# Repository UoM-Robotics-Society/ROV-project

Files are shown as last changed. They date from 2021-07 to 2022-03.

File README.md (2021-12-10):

# ROV-project

## Description 
This repository contains the software, hardware and 3D design for the ROV project.

## Project introduction and motivation
Goal is to create Remotely Operated Vehicle for underwater environments. ROV should :
- should operate safely in underwater environment up to reasonably low water depth ( construction should be waterproof, designed in mind to deal with the possibility of flooding)
- be able to be controlled by the User on ground station ( using something like GUI or physical devices like joystick/xbox controller etc. )
- provide useful data from sensors to User ( video feedback, attitude ( orientation ), other somehow relevant sensors )
- design should be flexible for possible modification in future 

## Diagram 
Whole system of the ROV is presented on the image below :
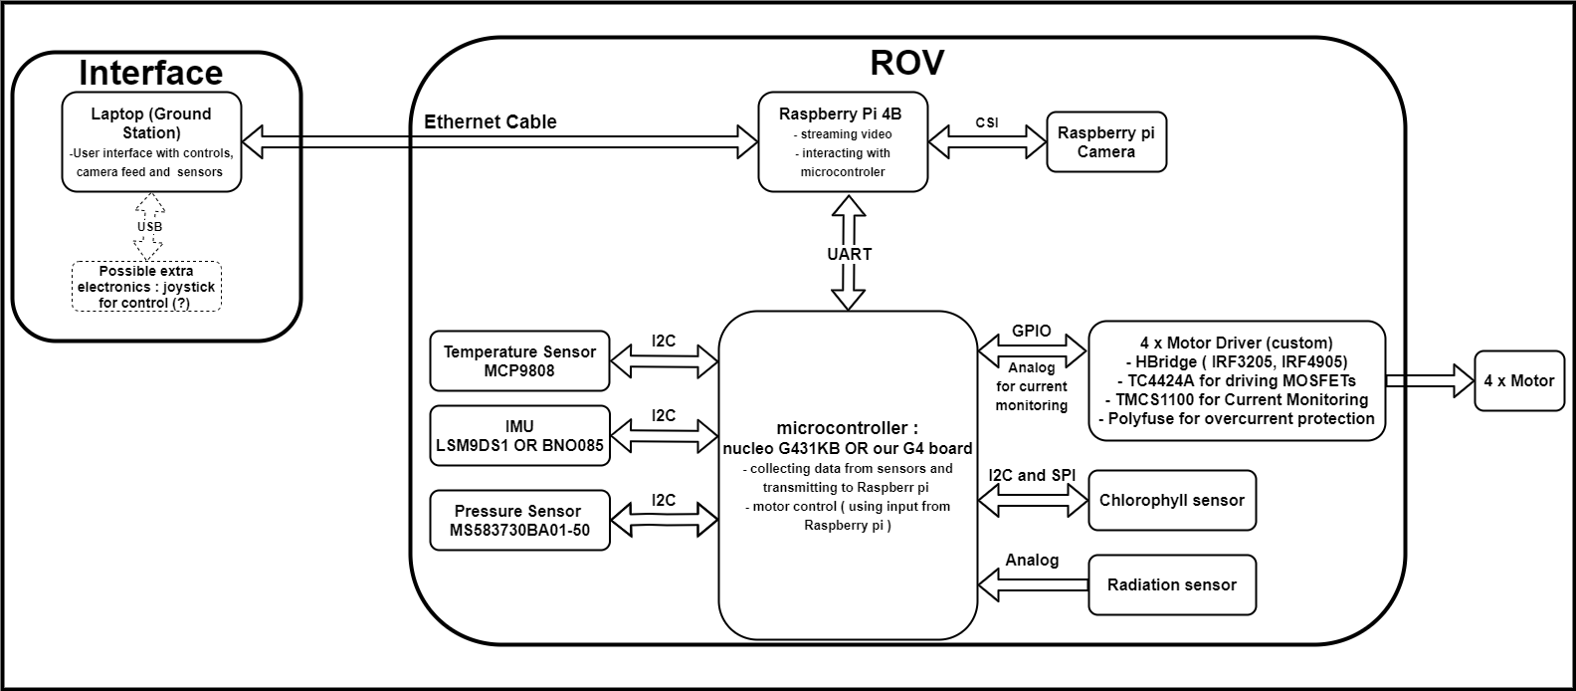
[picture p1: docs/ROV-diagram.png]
diagram


## Mechanical Design 
### Design
video of the model render

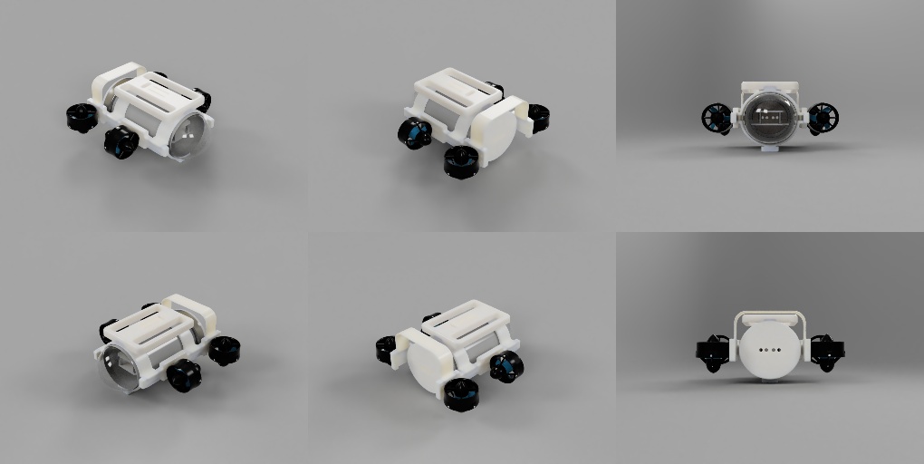
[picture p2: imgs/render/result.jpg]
stiched images of the mode


whole mechanical design is done by mechanical team of ROV team  
### Waterproofing

### Components Description 
#### Ground Station
- Main device with which User will interact will be laptop ( or other device to which we can connect Ethernet cable and will provide easy interaction ). Using laptop/other workstation provides few benefits : 
    - Most of the "heavy stuff" will be done on the workstation that we can control and only necessary software will run in the actual ROV 
    - makes the system very flexible : lots of possible expansion in the future ( fancy control like joysticks ? We can create own device and plug to USB or add support for xbox controller. Some computer vision algorithms for the camera ? the workstation can have GPU on it, we can provide quite a lot of computation power ( rather than relying on raspberry pi or other single board computer ))

#### Communication
- Ethernet should allow fast ( Raspberry pi has 1Gbit Ethernet port ), reliable and long distance communication ( and works underwater since it's just a cable ). We can also use Ethernet to power the device ( "Power over Ethernet") 
-  All other communication within ROV uses standard and popular data transmission protocols 
-  According to David, possiblity of extension to wireless 

Raspberry pi connected to laptop over 20 meter ethernet cable. Currently just streams video ( 1080p) over MQTT, bandwidth test below : 
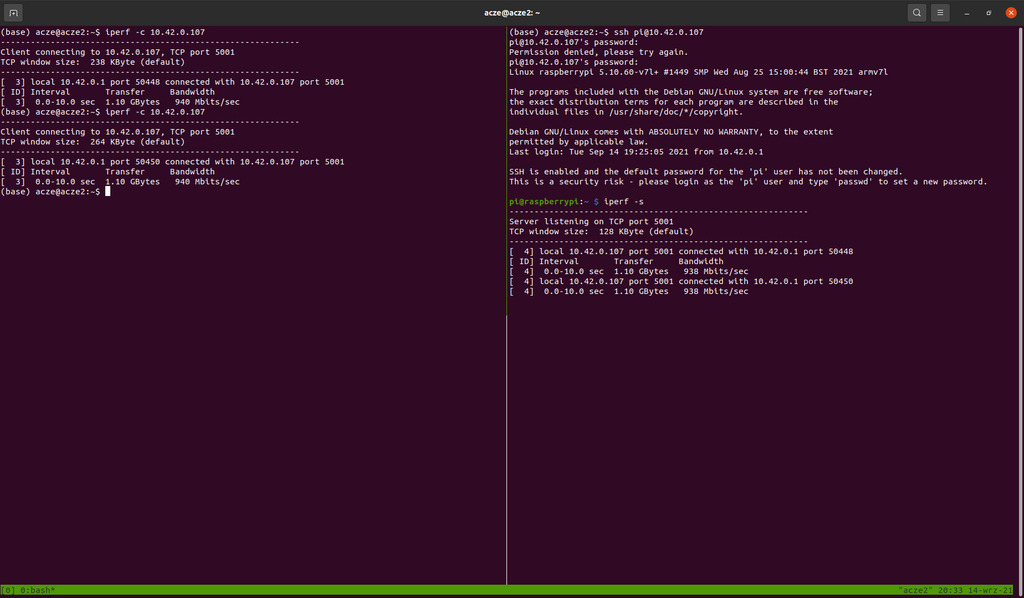
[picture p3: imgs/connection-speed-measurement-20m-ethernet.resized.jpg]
940 Mbit/s for communication


### Single Board Computer ( Raspberry Pi 4b)
- Extremely popular platform with support for good quality, real time video streaming and interacting with hardware ( using Serial communication ). Great community support and very fast to learn ( also Computer Science departament uses it in teaching )
- Can be programmed in few languages ( C, C++, python, probably others ), although python is used for the fast and easy development ( limitations of python like GIL can be removed by using multiprocessing etc.). 

### Microcontroller ( STM32G4)
- Microcontroller from new G4 line from STMicroelectronics. Not popular line, not "battle-tested" but cheap, high-performance microcontroller with lots of peripherals and can be programmed in Mbed Environment or HAL. Although there are popular choices ( pico's, arduino atmega's, ESP32's other stm's) it can be great opportunity to learn new platform that seems to be targeted for more industrial applications ( and overall learn something new and fun). Other than that, it has lots of features per pound ( 3.5 pound before chip shortage). The design doesn't realy that much on the microcontroller ( it requires few good timers, I2C, UART, SPI, reasonable ADC, most of the microcontrollers provide that)  so we can change to other platform if the chosen microcontroller won't prove it's worth. 

Current microcontroller board :<br>
STM32 G4 board
<br><br>
Render of the final board that will go hopefully in the final design
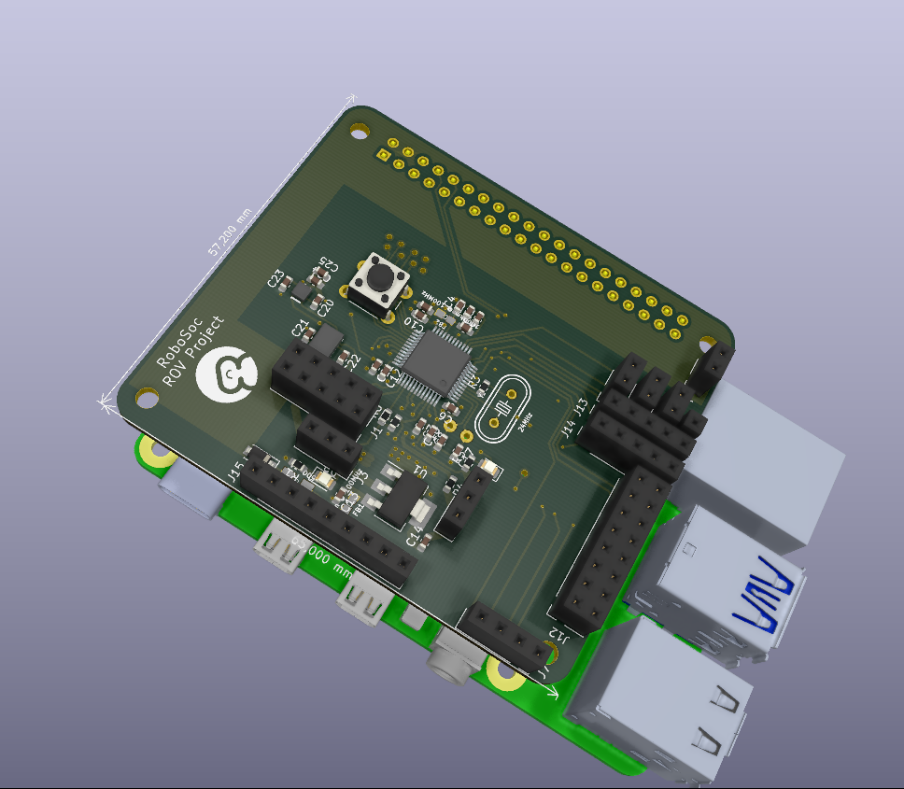
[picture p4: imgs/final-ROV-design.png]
STM32 G4 board


### Motors
- Lots of possible choices ( We orderd the dual shaft ,mabuchi like(DC motor),~30W from robotshop). Custom driver created for the motors using Hbridge circuit. Main drawback is that we need to solder/design/debug it but advantage is that it provides quite a bit of extra features that we included in our design : overcurrent protection ( using polyfuse ), high amperage and reasonably low power losses ( dependent on mosfets ), protection of Microcontroller pins ( using Mosfet driver to drive large mosfets from Hbridge) and current monitoring ( output voltage of TMCS1100 sensor is proportional to the current that flows through the mosfets). All of the features could possibly help us debugging, monitoring and hopefully help with safety when dealing with large motors.
-  Possibility of adding encoders in the future 

Current Motor driver : <br>
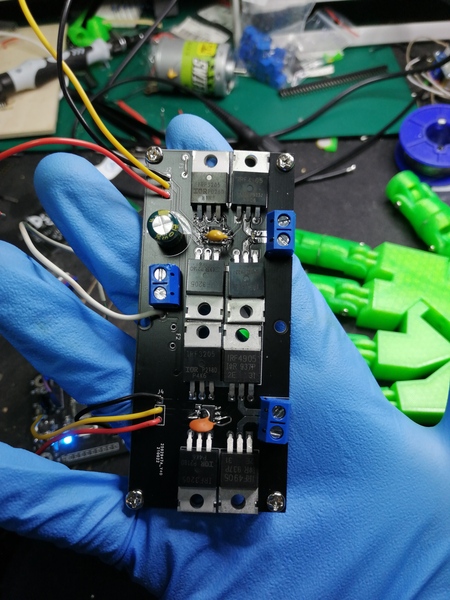
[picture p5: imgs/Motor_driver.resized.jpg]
Motor driver


### Sensors 
- Other than driving platform we wanted to provide range of measurements:
  -  Temperature sensor is standard. 
  -  Pressure sensor is not popular sensor, designed specifically for underwater environment ( up to 300m ) which provides high resolution ( and it's low cost compared to other underwater sensors ). 
  -  MARG sensor ( accelerometer, gyroscope, magnetometer). Using the data we can use AHRS algorithm ( experimented with Madgwick Filter which will be probably used in the design) we can visualize the orientation of the ROV on display on the laptop / ground station [Madgwick Report](https://www.x-io.co.uk/res/doc/madgwick_internal_report.pdf).
  -  Chlorophyll sensor. Custom sensor using the fluorescence measurement that should allow us to estimate the chlorophyll concentration. Chlorophyll concentration helps scientists to estimate health of the lake/other water containers [TODO point to document with more details].
  -  Radiation sensor : was in the first design because of initial project idea from Sellafield. Seems like challenging project and cool expansion to the project. Initial design created from the Elektor magazine article about Radiation detection. General reference used for it was "Radiation detection and measurement" and [opengeiger](http://www.opengeiger.de/index_en.html) website

Sensors : <br>
Chlorophyll sensor : <br>
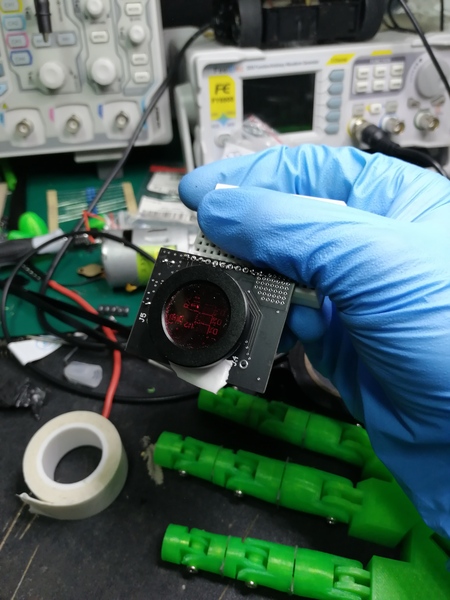
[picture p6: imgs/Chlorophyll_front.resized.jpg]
Chlorophyll sensor front

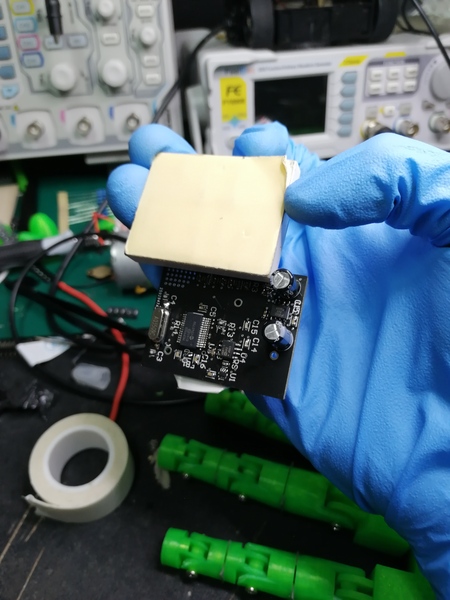
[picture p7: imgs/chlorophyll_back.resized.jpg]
Chlorophyll sensor back


Pressure Sensor : <br>
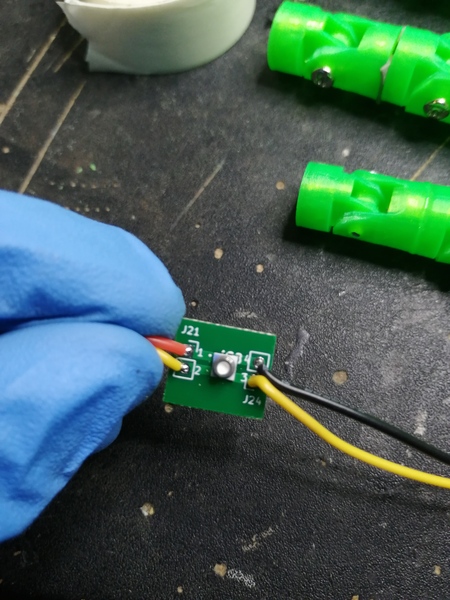
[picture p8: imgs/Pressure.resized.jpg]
Pressure sensor


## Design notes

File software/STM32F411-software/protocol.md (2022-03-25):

## Serial communication with the STM32 

|1 Byte | 2 Byte |3 Byte|4 Byte|
|---|---|---|---|
|peripheral|config|data[15:7]|data[7:0]|

### Peripheral
|Peripherals|
|---|
| 0x00 : STM32 config | 
| 0x01 : Motor Control |
| 0x02 : LED |
| 0x03: Leak detection |
| 0x04 : Temperature sensor |
| 0x05 : Pressure sensor |
| 0x06 : Radiation sensor |
| 0x07 : chlorophyll sensor |

### Config
|7th bit|6th bit|5th bit|4th bit|3th bit|2th bit|1th bit|0th bit|
|---|---|---|---|---|---|---|---|
|Write 0<br>Read 1|type bit 1|type bit 0|channel bit 4|channel bit 3|channel bit 2|channel bit 1|channel bit 0|

### Examples
|command|purpose|CLI command|
|---|---|---|
|0x00, 0b00000000, 0x00, 0x00| echo|stm32 write 0 0 0| 
|0x00, 0b00000001, 0x00, 0x01| toggle LED|stm32 write 0 1 0|
|0x01, 0b00000000, 0x00, 0x00| write x to motor channel 0|motor write 0 0 x| 
|0x01, 0b00000001, 0x00, 0x00| write x to motor channel 1|motor write 0 1 x| 
|0x01, 0b00000010, 0x00, 0x00| write x to motor channel 2|motor write 0 2 x| 

    STM32 Config
        Channel : 0
            description : Echo back the message
        Channel : 1
            description : Toggle LED
            data:
                0 : turn off the LED
                1 : turn on  the LED
                2 : toggle the LED 
        Channel : 2
            description:
    Motor Control:
        Channel : 0
            description : Thruster nr 1
            Type:
                0 : write value to CRT
                1 : data represents x / 10000 of duty cycle ( max x = 10000. 100% duty cycle
                2 : set frequency
            data:
                interpretation dependent on type above
        Channel : 1
            description : Thruster nr 2
            Type:
                0 : write value to CRT
                1 : data represents x / 10000 of duty cycle ( max x = 10000. 100% duty cycle
                2 : set frequency
            data:
                interpretation dependent on type above
        Channel : 2
            description : Thruster nr 3
            Type:
                0 : write value to CRT
                1 : data represents x / 10000 of duty cycle ( max x = 10000. 100% duty cycle
                2 : set frequency
            data:
                interpretation dependent on type above
        Channel : 3
            description : Thruster nr 4
            Type:
                0 : write value to CRT
                1 : data represents x / 10000 of duty cycle ( max x = 10000. 100% duty cycle
                2 : set frequency
            data:
                interpretation dependent on type above
    LED Control:
        Channel 0:
            description : control of while LED 1 
            Type : 
                0 : write value to CRT
                1 : 
            data:
                decrpition: interpretation depends on the type

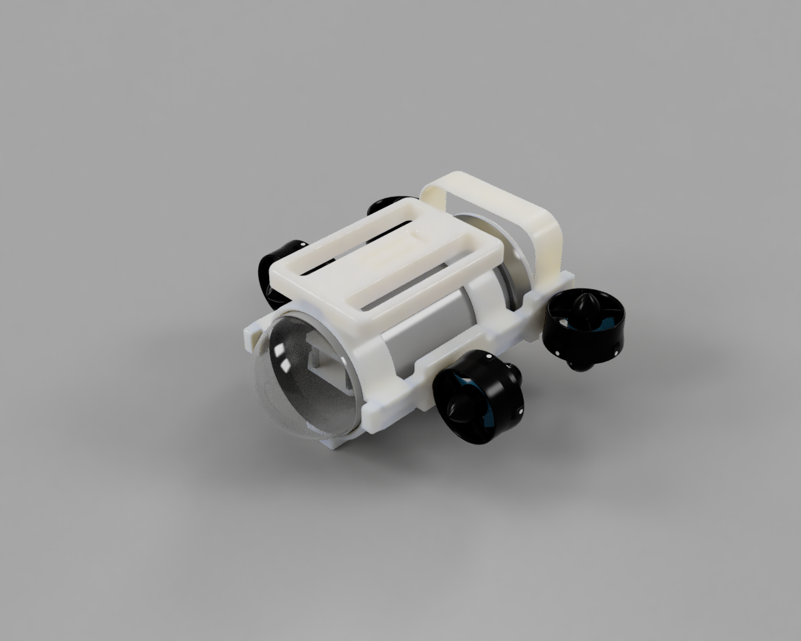
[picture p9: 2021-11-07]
imgs/pres/Front_Right.png

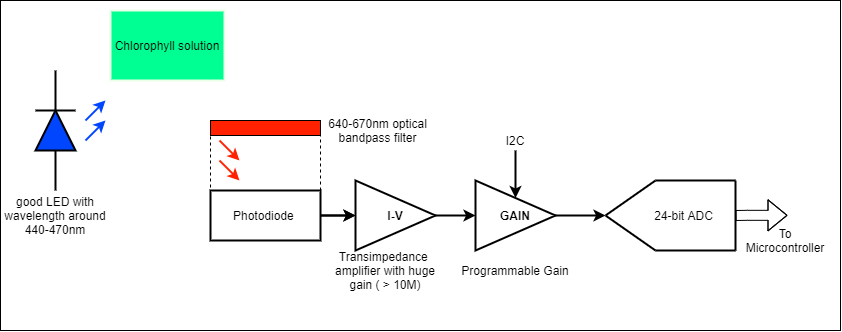
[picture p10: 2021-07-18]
docs/chlorophyll-sensor.png

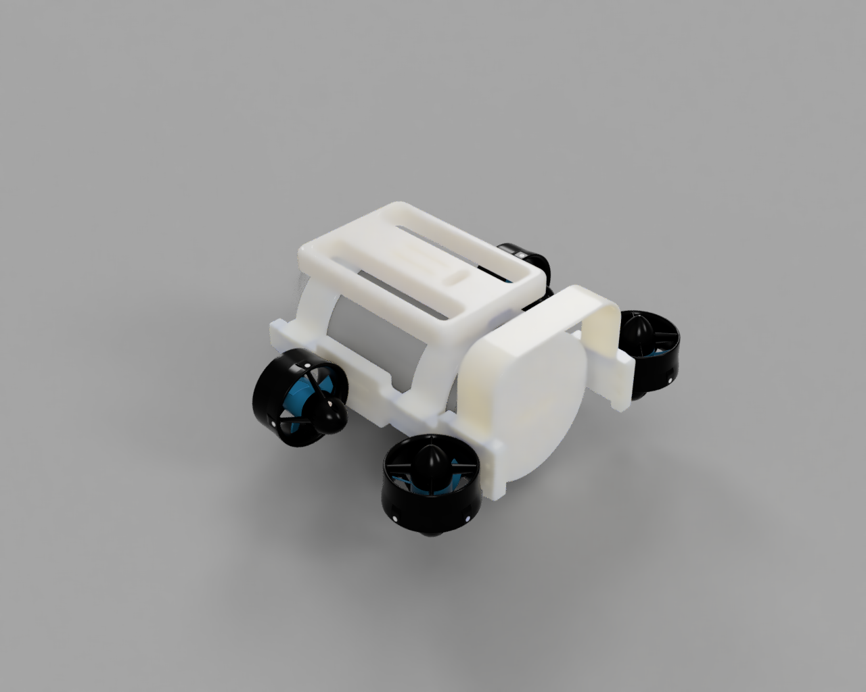
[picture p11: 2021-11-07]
imgs/render/Back_Left.png

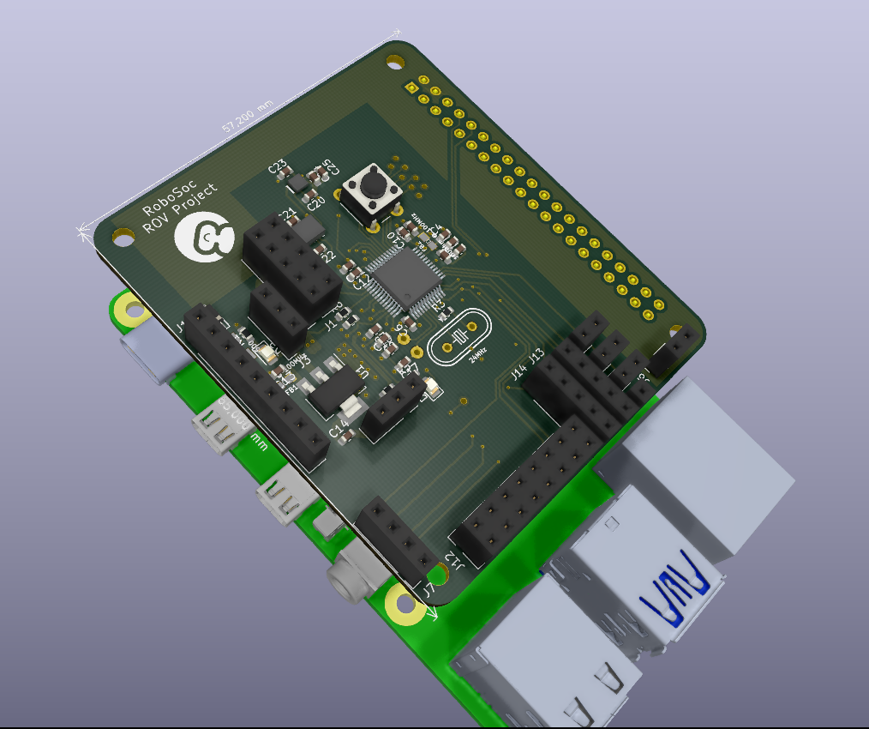
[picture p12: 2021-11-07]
imgs/pres/final_board.png

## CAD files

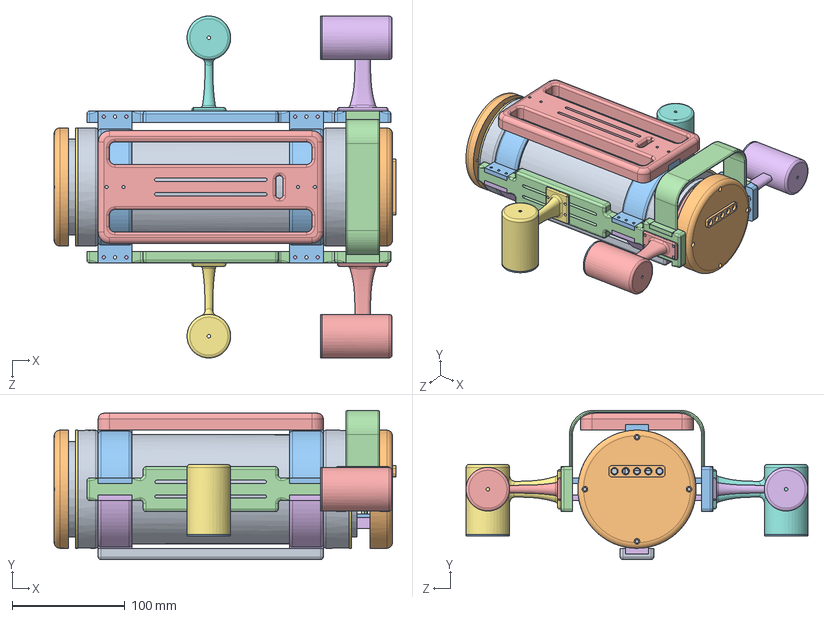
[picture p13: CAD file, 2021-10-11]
mechanical-design/ROV Design/ROV MK 4.SLDASM
303.5 x 132.5 x 303.8 mm
Cylinder Front Lid
Side Frame Right
Side Frame Left
Motor Connector Rod left
Motor Connector Rod Right
Motor Up Connector Rod Left
Motor Up Connector Rod Right
Bottom Frame
Cylinder Back Lid Cap
Cylinder Back Lid Bottom Plate
25 mm Standoff x 4
Cylinder Back Lid Top Plate
Cylinder Back Lid Bottom Plate Holder
Raspberry Standoff x 4
Raspberry Camera Housing
Raspberry Camera
Chlorophyll Sensor
Bracket Holder x 2
Bracket No Holder Back
Bracket Holder Botoom x 2
Rubber seal large 2 x 2
Rubber seal x 2
Glass
Rubber seal medium
Motor Cap x 4

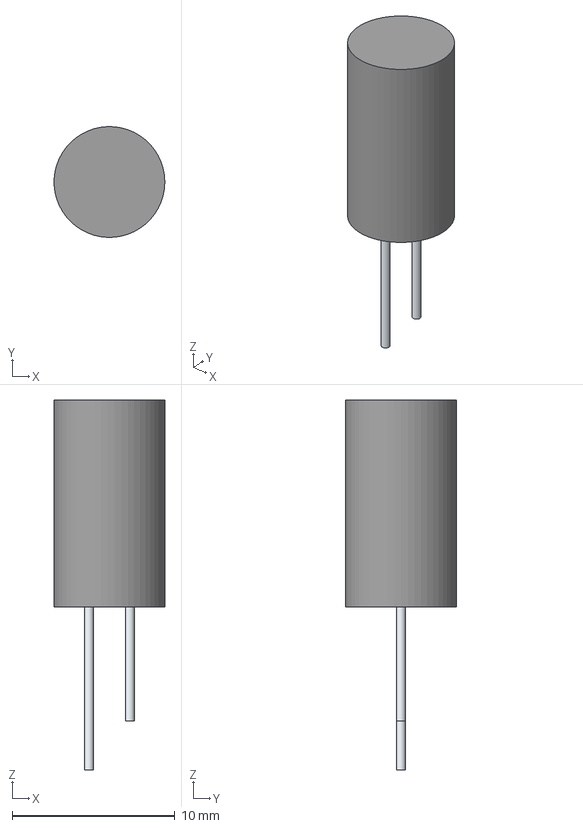
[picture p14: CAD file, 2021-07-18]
hardware/chlorophyll_sensor/design/3d_cad/EEU-FR1E151.stp
6.79 x 6.80 x 22.7 mm
SimpleBody
Pin1
Pin2

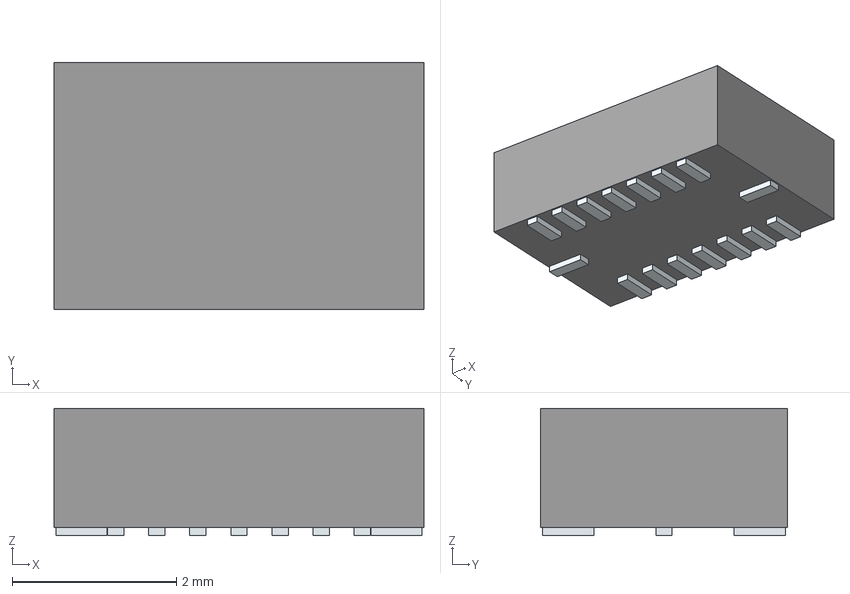
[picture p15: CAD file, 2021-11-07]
hardware/Final-G4-board/3d/BMI088.stp
4.50 x 3.00 x 1.55 mm
Pins

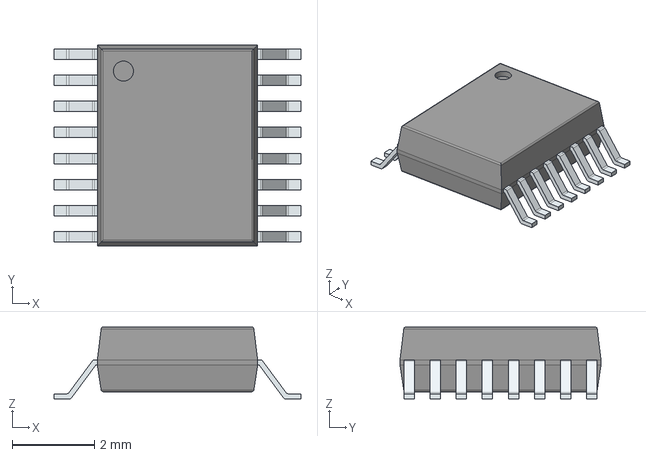
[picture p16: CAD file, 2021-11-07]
hardware/radiation_sensor/extra/3D/LTC6242HVCGN#PBF.stp
6.01 x 4.89 x 1.75 mm
PinsArrayLR

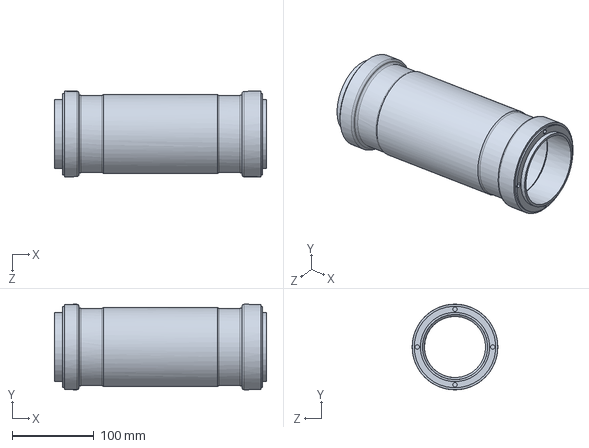
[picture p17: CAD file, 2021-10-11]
mechanical-design/ROV Design/Cylinder.SLDPRT
260.0 x 105.0 x 105.0 mm

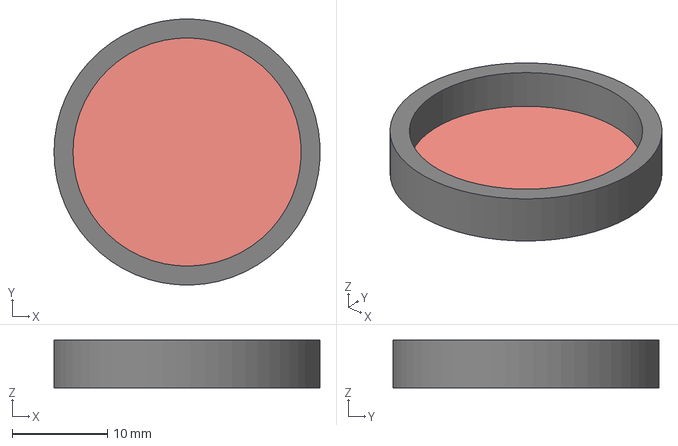
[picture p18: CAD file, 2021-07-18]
hardware/chlorophyll_sensor/design/3d_cad/filter v1.step
28.0 x 28.0 x 5.00 mm

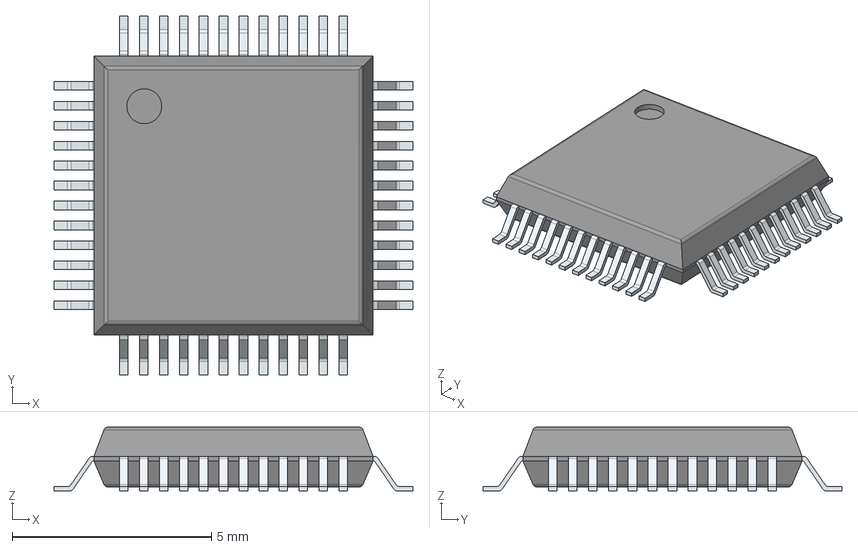
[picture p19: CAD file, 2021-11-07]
hardware/Final-G4-board/3d/STM32G431C6T6.stp
9.00 x 9.00 x 1.60 mm
PinsArrayLR
PinsArrayTB

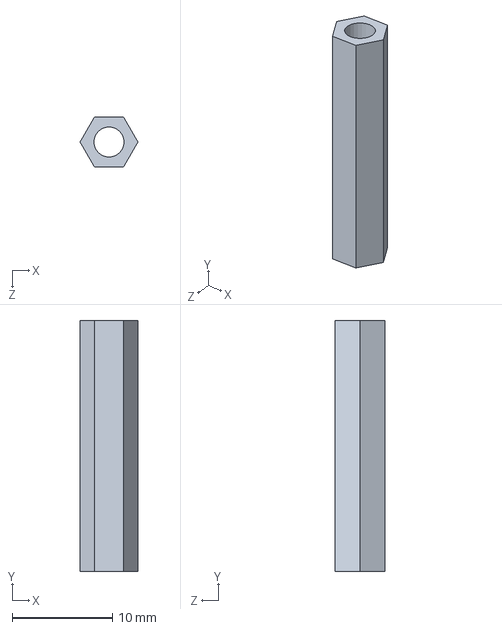
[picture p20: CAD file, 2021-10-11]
mechanical-design/ROV Design/25 mm Standoff.SLDPRT
5.77 x 25.0 x 5.00 mm

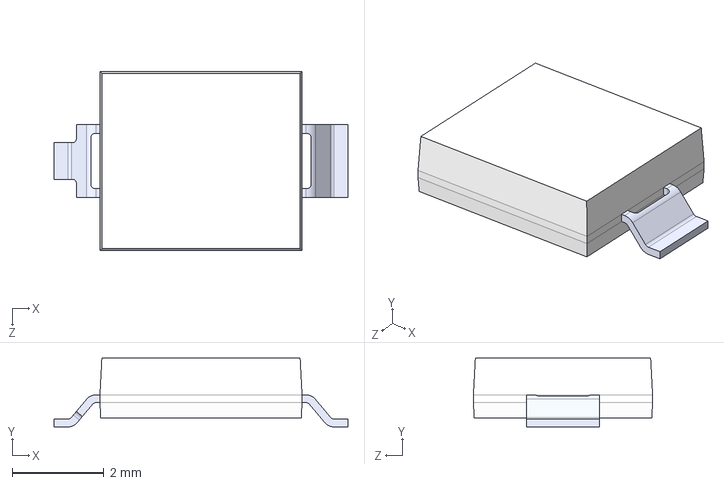
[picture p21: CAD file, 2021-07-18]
hardware/chlorophyll_sensor/design/3d_cad/VBPW34S--3DModel-STEP-56544.STEP
6.40 x 1.50 x 3.90 mm

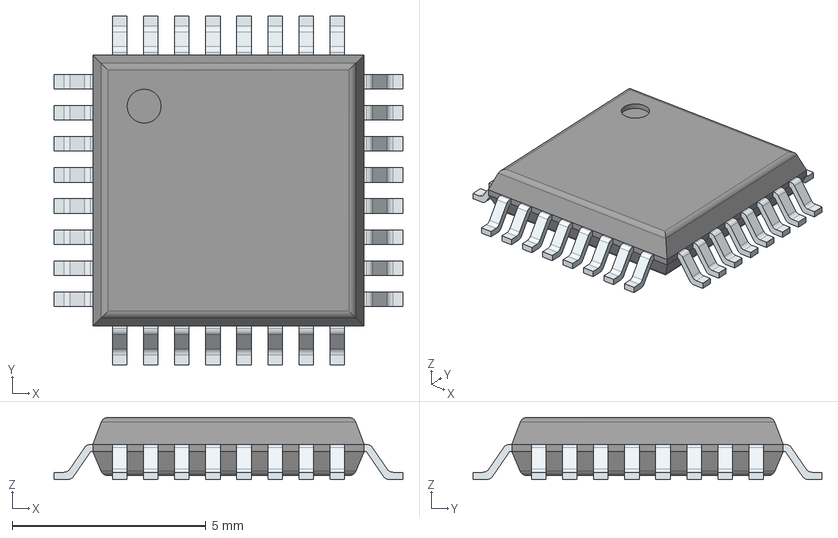
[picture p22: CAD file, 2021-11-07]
hardware/Final-G4-board/3d/STM32G431K8T6.stp
9.00 x 9.00 x 1.60 mm
PinsArrayLR
PinsArrayTB

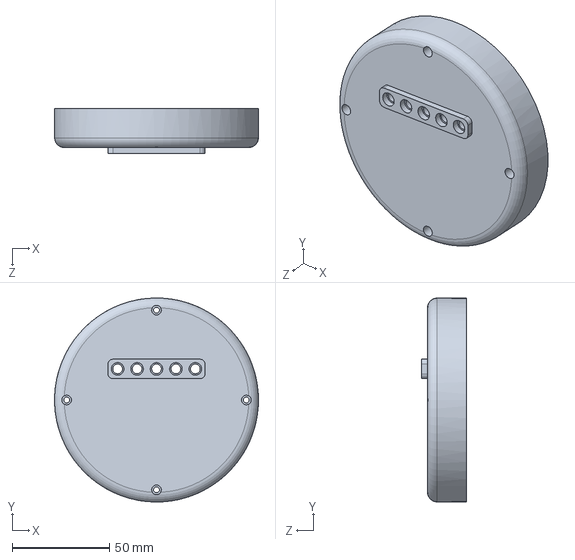
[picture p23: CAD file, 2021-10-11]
mechanical-design/ROV Design/Cylinder Back Lid Cap.SLDPRT
105.0 x 105.0 x 23.0 mm

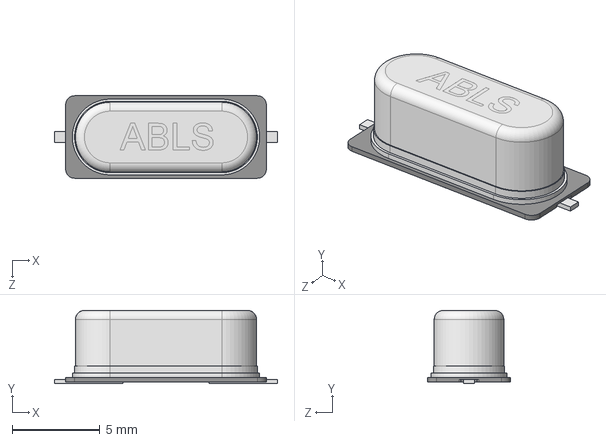
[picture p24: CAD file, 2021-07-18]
hardware/chlorophyll_sensor/design/3d_cad/ABLS.STEP
12.7 x 4.17 x 4.70 mm

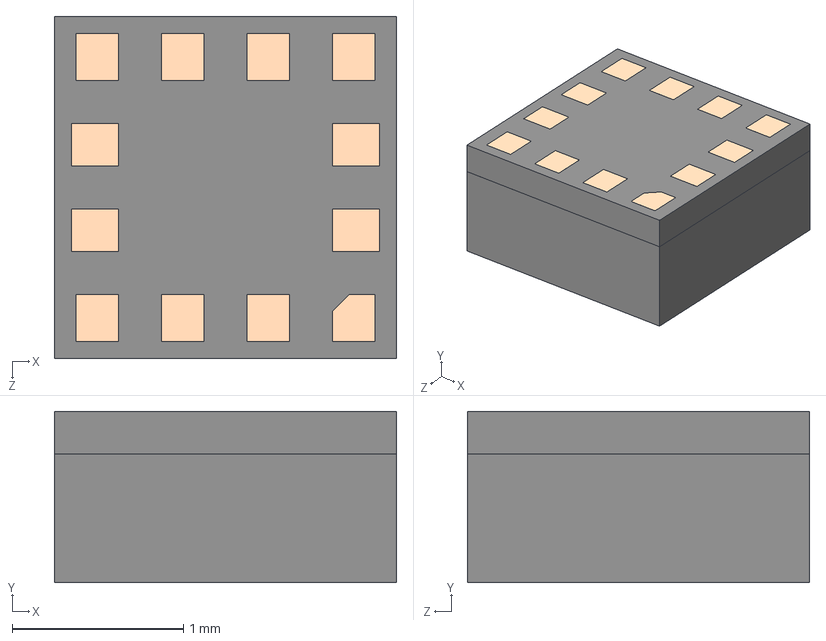
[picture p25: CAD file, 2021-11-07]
hardware/Final-G4-board/3d/LSM303AGRTR.stp
2.00 x 1.00 x 2.00 mm

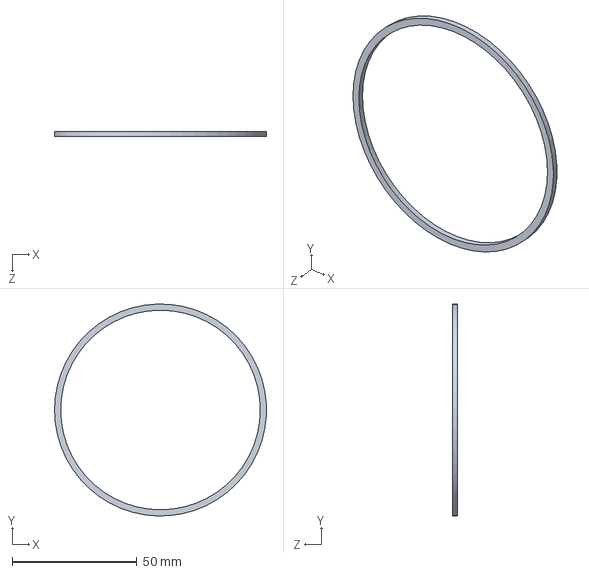
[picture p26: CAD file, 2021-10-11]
mechanical-design/ROV Design/Rubber seal medium.SLDPRT
85.0 x 85.0 x 2.00 mm

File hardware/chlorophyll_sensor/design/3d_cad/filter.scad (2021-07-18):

color("black", 1)
difference()
{
    cylinder(d=28, h=4, $fn=100);
    translate([0,0,-0.1])
    cylinder(d=24, h=4.5, $fn=100);
}

translate([0, 0, 2.7])
color("red", 0.3)
cylinder(d=25,h=1, $fn=100);

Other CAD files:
hardware/chlorophyll_sensor/design/3d_cad/User Library-VEMD1060X01-1.STEP
hardware/Final-G4-board/3d/IIS2MDCTR.stp
mechanical-design/ROV Design/Raspberry Standoff.SLDPRT
hardware/chlorophyll_sensor/design/3d_cad/filter.stl
hardware/chlorophyll_sensor/design/3d_cad/SFH_2713_20200701_geometry.STEP
hardware/chlorophyll_sensor/design/3d_cad/m20-97311xx_asm.stp
hardware/radiation_sensor/extra/3D/LTC6242HVCGN#PBF.stl
mechanical-design/ROV Design/Bottom Frame.SLDPRT
mechanical-design/ROV Design/Bracket Holder Botoom.SLDPRT
mechanical-design/ROV Design/Bracket Holder.SLDPRT
mechanical-design/ROV Design/Bracket No Holder Back.SLDPRT
mechanical-design/ROV Design/Cylinder Back Lid Bottom Plate Holder.SLDPRT
mechanical-design/ROV Design/Cylinder Back Lid Bottom Plate.SLDPRT
mechanical-design/ROV Design/Cylinder Back Lid Top Plate.SLDPRT
mechanical-design/ROV Design/Cylinder Front Lid.SLDPRT
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

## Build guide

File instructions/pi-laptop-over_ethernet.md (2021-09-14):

# Connecting
1. Connect via Ethernet cable pi and laptop
2. Settings -> Network -> Wired Gearbox -> IPv4 -> Shared to other computers
3. ```ip a ```  and get the ip address from ethernet interface
3. ```nmap -n -sP 10.42.0.255/24``` ( or any other address)
4. get the ip address from above and ```ssh pi@<ip address of above>```

# Bandwidth test
1. ```sudo apt-get install iperf```
2. On raspberry pi ```iperf -s```
3. On laptop ```iperf -c <ip address of raspberry pi>```

# Results 

|Cabel Length|Bandidth|
|---|---|
|0.25m|942 Mbits/sec|
|20m|940 Mbits/sec|

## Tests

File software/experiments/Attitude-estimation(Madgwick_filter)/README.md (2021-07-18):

# IMU [ Work in progress ] !
playing with 3d attitude estimation using Madgwick filter from https://courses.cs.washington.edu/courses/cse474/17wi/labs/l4/madgwick_internal_report.pdf , some other stuff included.

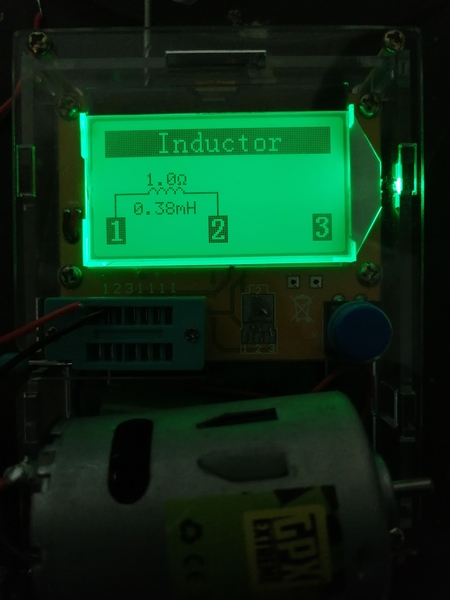
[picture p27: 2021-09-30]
imgs/motor_measurement.resized.jpg

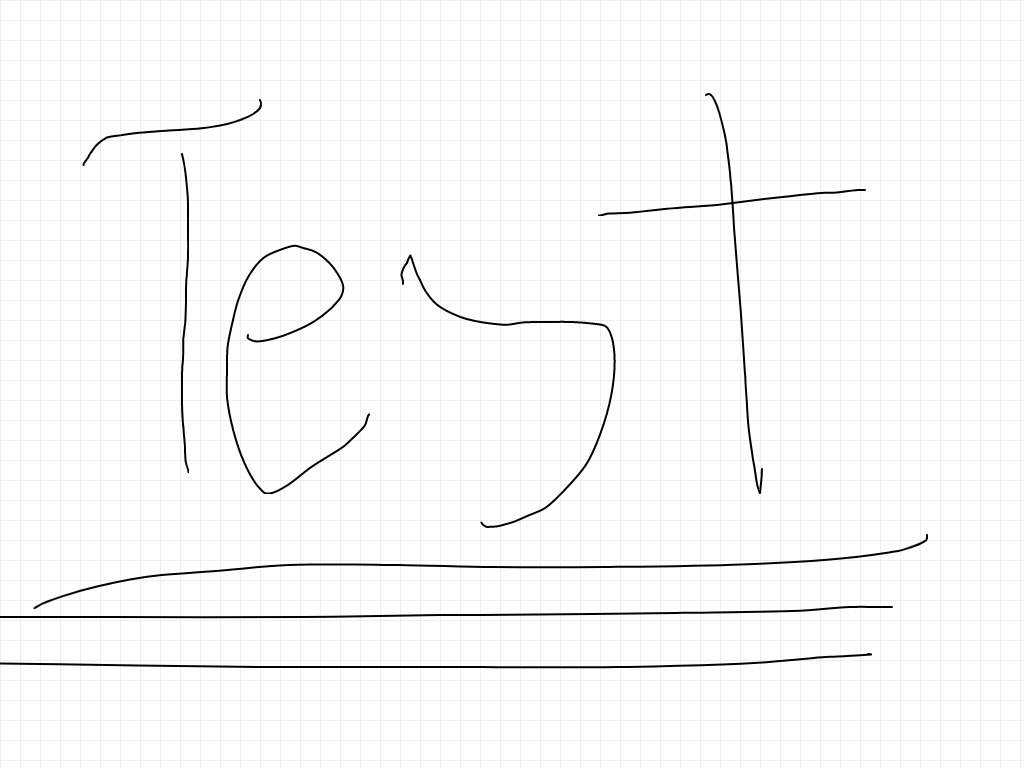
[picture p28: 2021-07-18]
software/pi-software/test/test.jpg

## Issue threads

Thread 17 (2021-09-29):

Final board

Ache17, 2021-09-29:
one single board ( or 2 ) that ties all electronics together. That should include :
- STM32 microcontroller
- Raspberry pi connector
- all the connectors for sensors
- Motor driver
- connector for raspberry pi camera
- any extra electronics ( BMS if we will be using battery, etc.  )

Closed 2022-02-01.

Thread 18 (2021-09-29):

Attitude Estimation

Ache17, 2021-09-29:
- Coding attitude estimation algorithm for the IMU
- Currently we have the LSM9DS1 for the IMU and some not well working code.
- Worst case scenario BNO085 might be used

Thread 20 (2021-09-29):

Change motor driver from kicad to altium

Ache17, 2021-09-29:
EEE teaches altium designer, it's industry standard so we need to port from kicad to alitum.

Closed 2022-02-01.

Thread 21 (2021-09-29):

Change STM32 board from kicad to altium

Ache17, 2021-09-29:
EEE teaches altium designer, it's industry standard so we need to port from kicad to alitum.

Closed 2022-02-01.

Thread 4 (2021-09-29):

Recreate setup in Lab and document it

Ache17, 2021-09-29:
- run Rasbperry pi software ( video streaming )
- run MQTT broker on raspberry pi
- connection to STM32 board
- 20m ethernet cable ( could be smaller but not smaller then 2 m)
- Connection to motor driver ( and test motor driver )

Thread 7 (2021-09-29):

Proper evaluation of the chlorophyll sensor

Ache17, 2021-09-29:
The chlorophyll sensor is on the github and is designed in altium.
It works but we need a proper evaluation how well it performs ( have a LED ~ 450nm flash to the water + (bioethanol + spinach) solution and see the responses ).
We need also to resolder it because It was not possible to ship it for some reason.
Some minor adjustments in the hardware design.

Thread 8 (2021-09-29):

Writing proper communication between STM32 and Raspberry pi

Ache17, 2021-09-29:
right now it's a bit messy, we need to correct it and do it right.

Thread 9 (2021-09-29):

Sending the control signals ( Drone Controller, joystick, xbox controller ) to the python server

Ache17, 2021-09-29:
Passing the steering data to python server so it can be transmitted to raspberry pi, decoded there and send to STM32.

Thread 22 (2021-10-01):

Constant current driver for LEDs

Ache17, 2021-10-01:
the feedback from camera will be probably quite blurry and dark.
It has to drive the higher power LEDs ( 1-3W ) and must be steered from microcontroller pin.

Ache17, 2022-02-04:
created basic high power LED driver (up to ~400 mA, can be dimmed by PWM signal from 100-200Hz  )  7419e89d27d99baf2a939559d8adaced86e9520d

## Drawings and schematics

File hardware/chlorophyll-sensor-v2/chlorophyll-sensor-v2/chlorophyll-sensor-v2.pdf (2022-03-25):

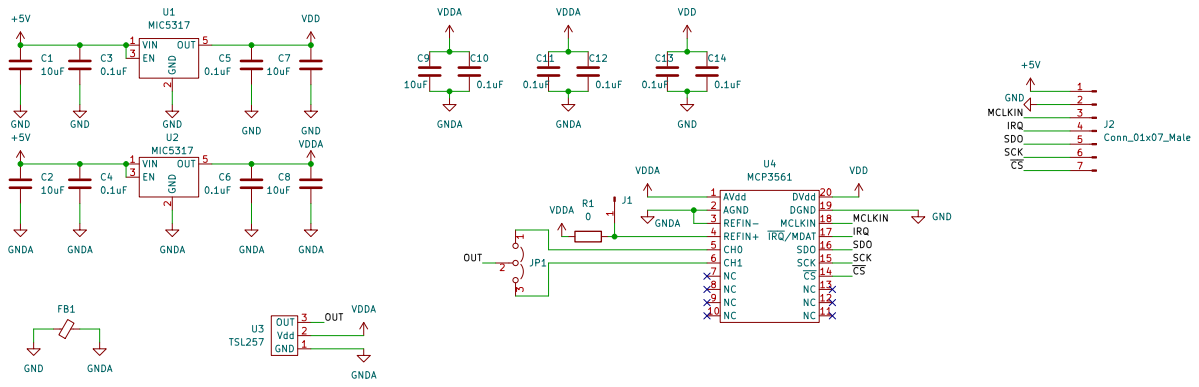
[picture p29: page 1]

2 EN 3 OUT 5 U1 MIC5317 GND 1 Vdd 2 OUT 3 U3 TSL257 C14
0.1uF GNDA C6

File: chlorophyll-sensor-v2.kicad_sch Sheet: /
Id: 1/1 Title:

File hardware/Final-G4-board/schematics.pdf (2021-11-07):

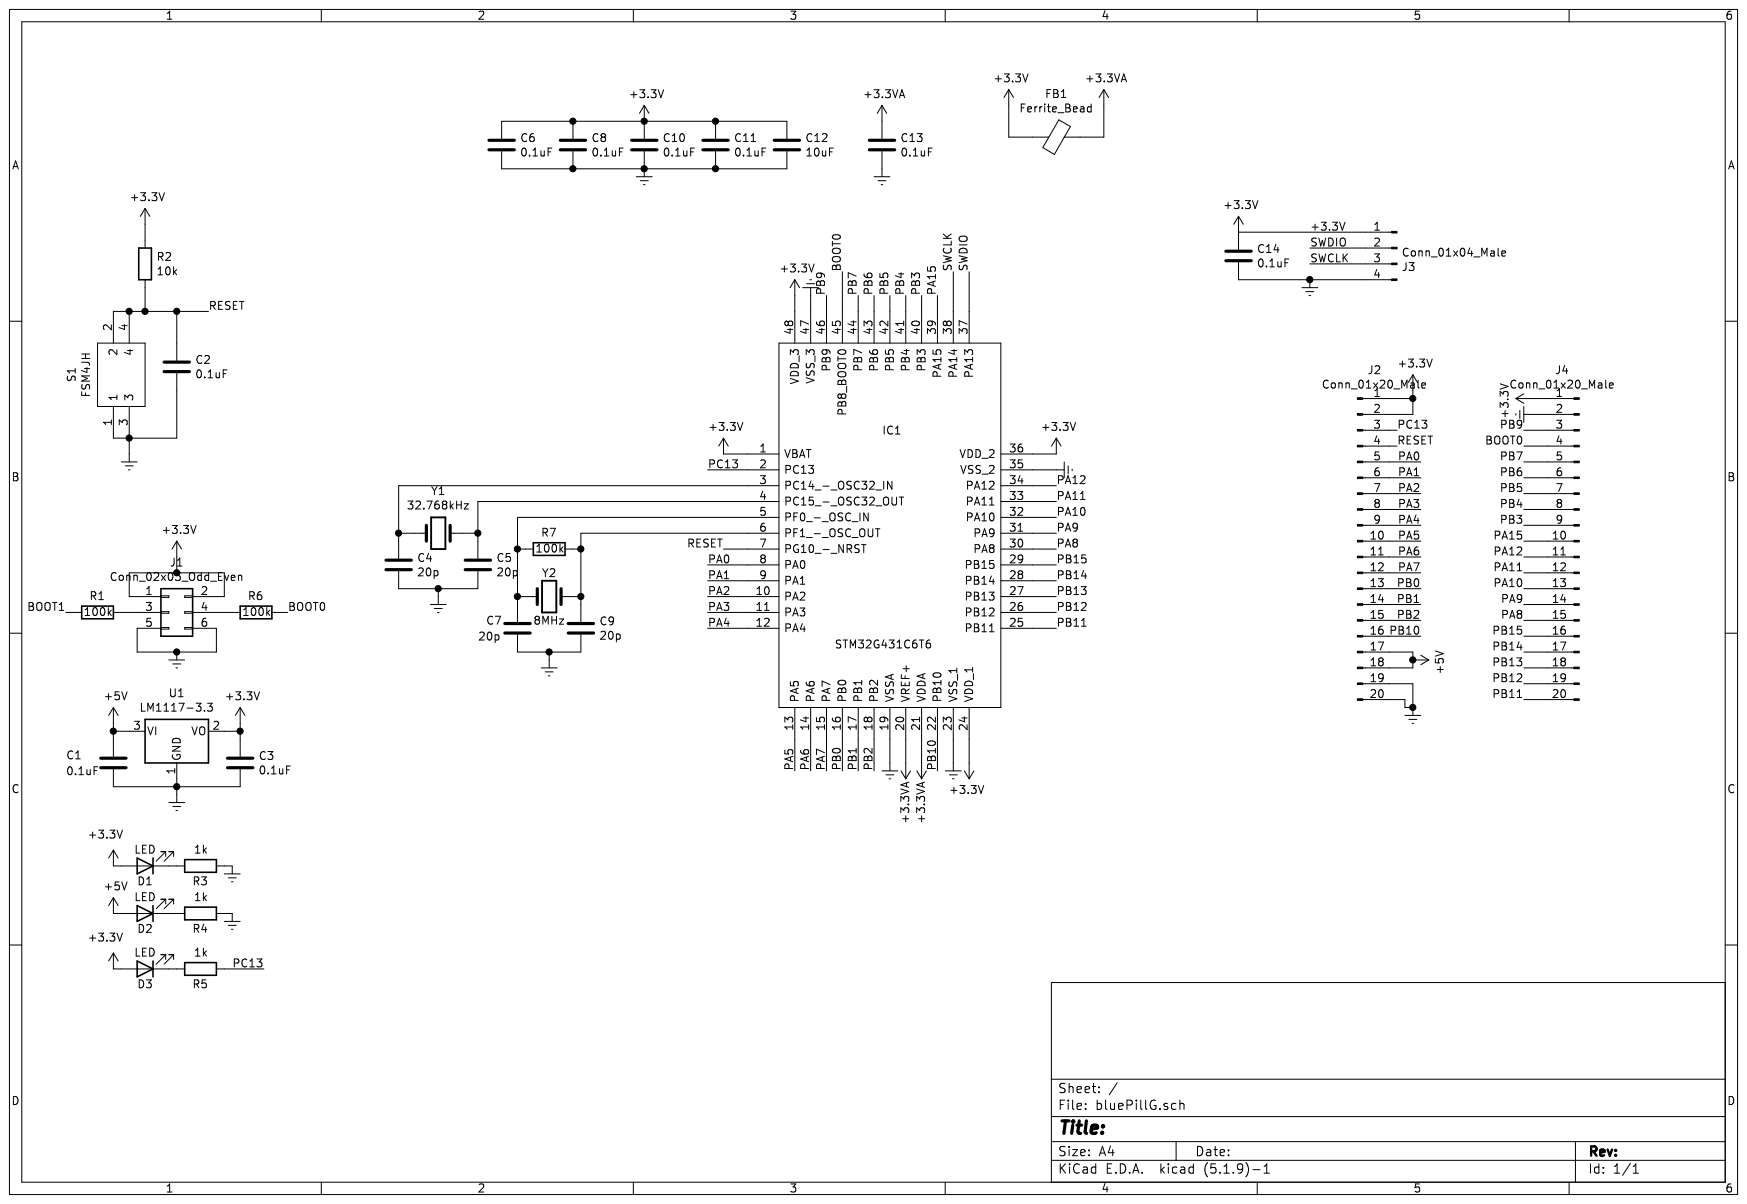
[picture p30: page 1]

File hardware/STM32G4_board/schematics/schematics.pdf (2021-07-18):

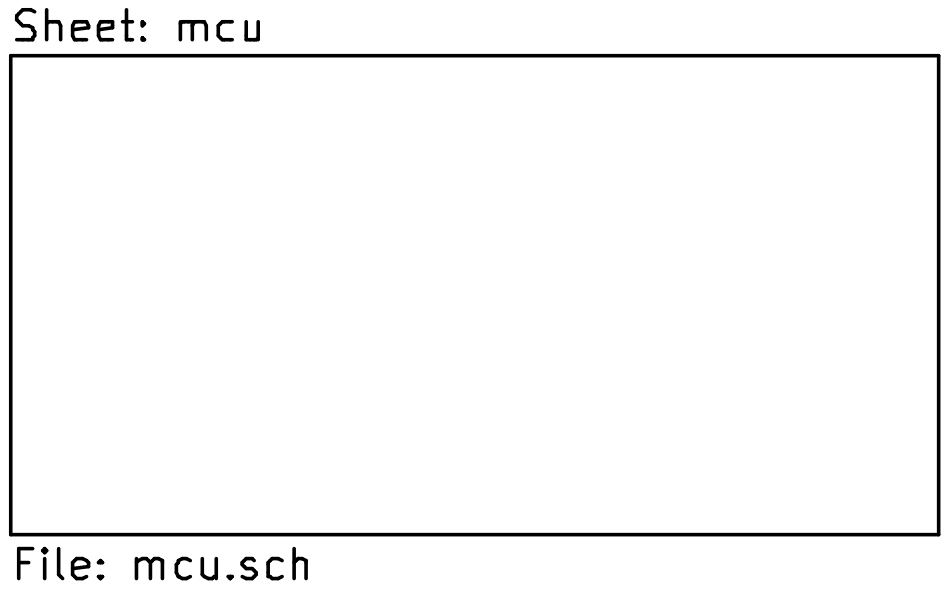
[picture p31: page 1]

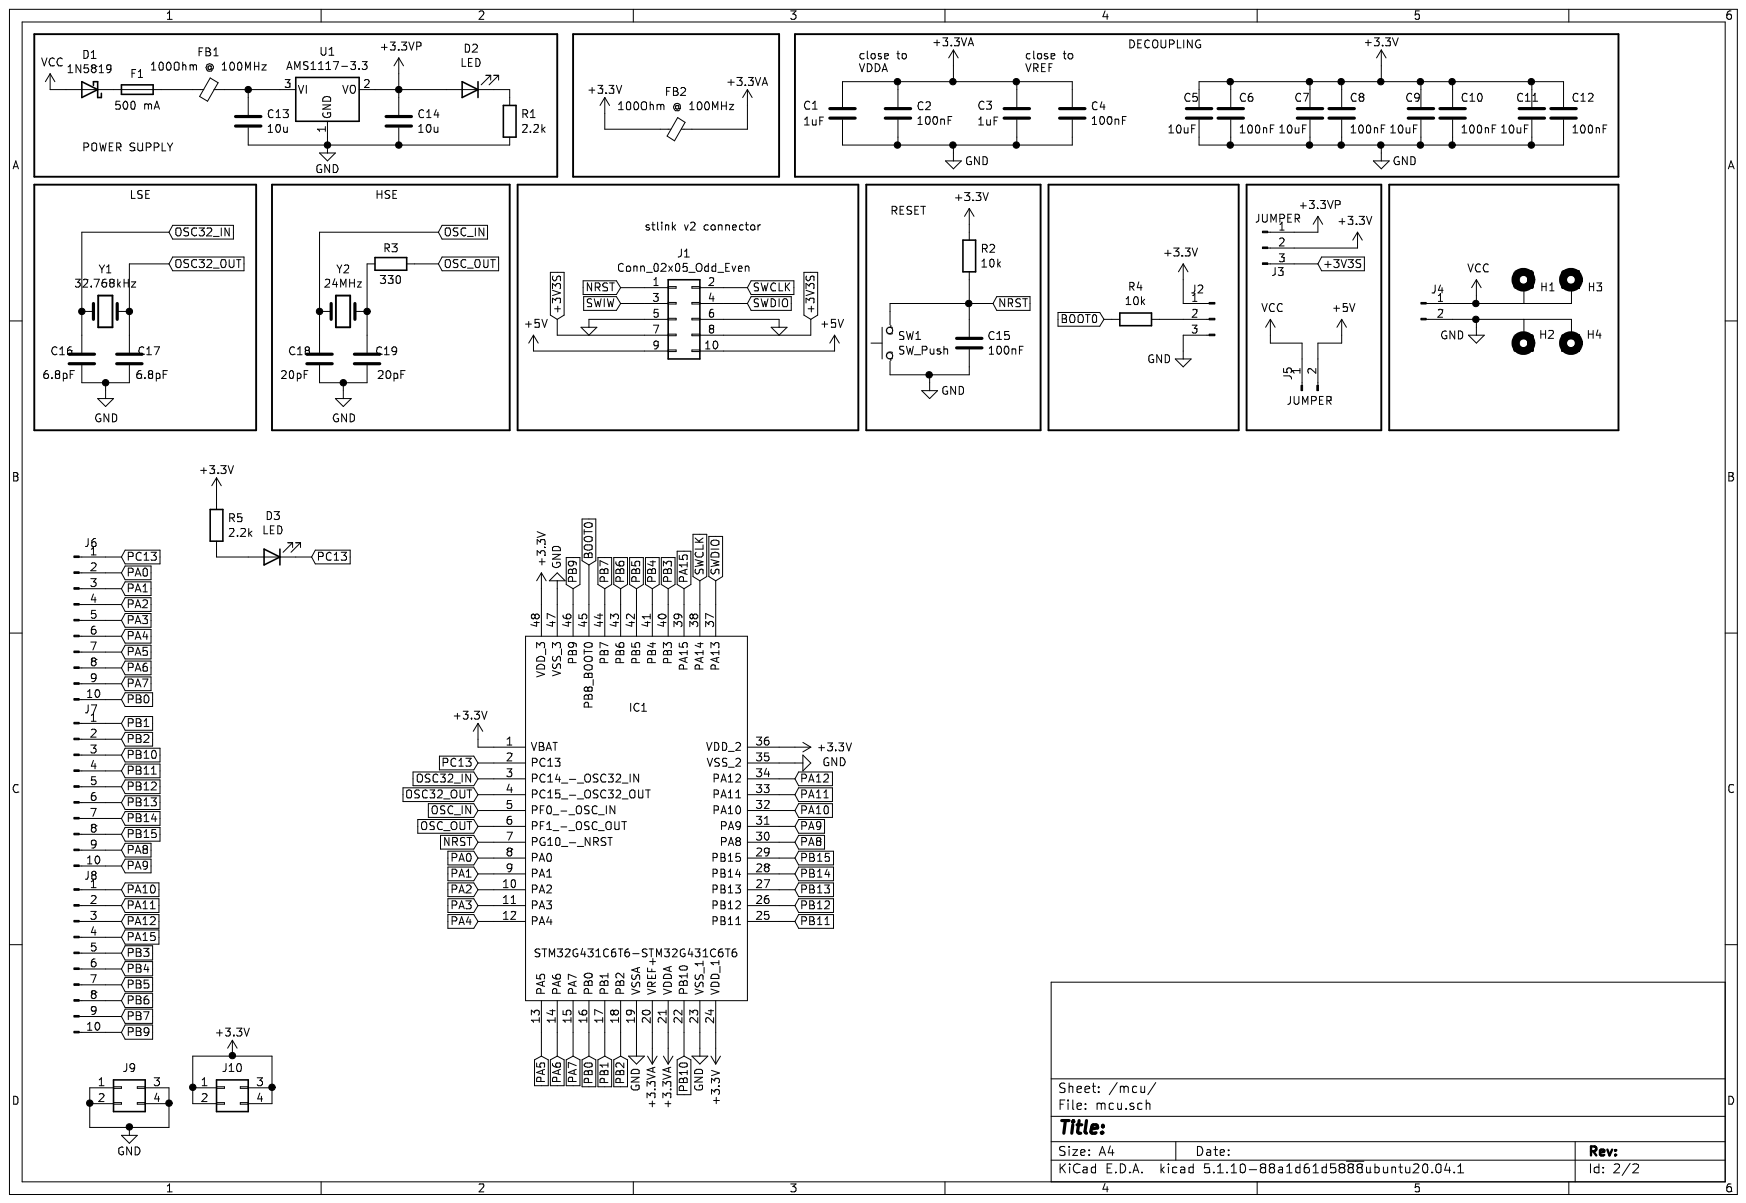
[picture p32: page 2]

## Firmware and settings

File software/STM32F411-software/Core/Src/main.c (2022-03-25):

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
/* Includes ------------------------------------------------------------------*/
#include "main.h"

/* USER CODE BEGIN Includes */
#include "communication.h"
#include "control.h"

/* USER CODE END Includes */

I2C_HandleTypeDef hi2c2;

SPI_HandleTypeDef hspi2;

TIM_HandleTypeDef htim2;
TIM_HandleTypeDef htim3;
TIM_HandleTypeDef htim4;
TIM_HandleTypeDef htim9;

TIM_TypeDef *motorPWMSignal;

UART_HandleTypeDef huart1;
UART_HandleTypeDef huart6;

/* USER CODE BEGIN PV */
char command[4];
char return_msg[4];
int maxCCRVal = 0;

/* USER CODE END PV */

void SystemClock_Config(void);
static void MX_GPIO_Init(void);
static void MX_USART1_UART_Init(void);
static void MX_I2C2_Init(void);
static void MX_SPI2_Init(void);
static void MX_TIM3_Init(void);
static void MX_TIM4_Init(void);
static void MX_TIM9_Init(void);
static void MX_USART6_UART_Init(void);
static void MX_TIM2_Init(void);
/* USER CODE BEGIN 0 */
void HAL_TIM_PeriodElapsedCallback(TIM_HandleTypeDef* htim)
{

}


void HAL_UART_RxCpltCallback(UART_HandleTypeDef *huart)
{
    struct command cmd;
    decodeMessage(&cmd, command, 4);

//  HAL_GPIO_TogglePin(LED_GPIO_Port, LED_Pin);
    HAL_UART_Receive_IT(&huart1, (uint8_t *)command, 4);
}


/* USER CODE END 0 */

/**
  * @brief  The application entry point.
  * @retval int
  */
int main(void)
{
  /* MCU Configuration--------------------------------------------------------*/

  /* Reset of all peripherals, Initializes the Flash interface and the Systick. */
  HAL_Init();

  /* Configure the system clock */
  SystemClock_Config();

  /* Initialize all configured peripherals */
  MX_GPIO_Init();
  MX_USART1_UART_Init();
  MX_I2C2_Init();
  MX_SPI2_Init();
  MX_TIM3_Init();
  MX_TIM4_Init();
  MX_TIM9_Init();
  MX_USART6_UART_Init();
  MX_TIM2_Init();
  /* USER CODE BEGIN 2 */

  // start timer 9
  HAL_TIM_Base_Start_IT(&htim9);

  /* USER CODE END 2 */

  /* Infinite loop */
  /* USER CODE BEGIN WHILE */

  HAL_UART_Receive_IT(&huart1, (uint8_t *)command, 4);

    for (int i = 0; i < 4; ++i) {
        HAL_GPIO_WritePin(LED_GPIO_Port, LED_Pin, GPIO_PIN_SET);
        HAL_Delay(250);
        HAL_GPIO_WritePin(LED_GPIO_Port, LED_Pin, GPIO_PIN_RESET);
        HAL_Delay(250);
    }

    command[0] = 'A';
    command[1] = 'B';
    command[2] = 'C';
    command[3] = 'D';

    motorPWMSignal = TIM2;

    HAL_TIM_PWM_Start(&htim2, TIM_CHANNEL_1);
    HAL_TIM_PWM_Start(&htim2, TIM_CHANNEL_2);
    HAL_TIM_PWM_Start(&htim2, TIM_CHANNEL_3);
    HAL_TIM_PWM_Start(&htim2, TIM_CHANNEL_4);

    maxCCRVal = 10000;
    TIM2->CCR1 = 5000;
    TIM2->CCR2 = 5000;
    TIM2->CCR3 = 5000;
    TIM2->CCR4 = 5000;


    int i = 0;
    while (1)
    {
    	for (i = 0; i < 10000; i += 200)
    	{
    		setMotorDutyCycle(i, 3);
    		HAL_Delay(19);
    	}
    	HAL_GPIO_TogglePin(LED_GPIO_Port, LED_Pin);
    /* USER CODE END WHILE */

    /* USER CODE BEGIN 3 */
    }
  /* USER CODE END 3 */
}

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


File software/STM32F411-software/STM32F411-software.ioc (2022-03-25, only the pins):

Mcu.UserName=STM32F411CEUx
PA0-WKUP.Signal=S_TIM2_CH1_ETR
PA1.Signal=S_TIM2_CH2
PA10.Signal=USART1_RX
PA11.Signal=USART6_TX
PA12.Signal=USART6_RX
PA13.Signal=SYS_JTMS-SWDIO
PA14.Signal=SYS_JTCK-SWCLK
PA15.GPIO_Label=ACCEL_INT
PA15.Signal=GPIO_Input
PA2.Signal=S_TIM2_CH3
PA3.Signal=S_TIM2_CH4
PA6.Signal=S_TIM3_CH1
PA7.Signal=S_TIM3_CH2
PA8.GPIO_Label=SPI_CS
PA8.Signal=GPIO_Output
PA9.Signal=USART1_TX
PB0.Signal=S_TIM3_CH3
PB1.Signal=S_TIM3_CH4
PB10.Signal=I2C2_SCL
PB12.GPIO_Label=LED3
PB12.Signal=GPIO_Output
PB13.Signal=SPI2_SCK
PB14.Signal=SPI2_MISO
PB15.Signal=SPI2_MOSI
PB2.GPIO_Label=LED2
PB2.Signal=GPIO_Output
PB3.Signal=I2C2_SDA
PB4.GPIO_Label=GYRO_INT
PB4.Signal=GPIO_Input
PB5.GPIO_Label=MAG_INT
PB5.Signal=GPIO_Input
PB6.Signal=S_TIM4_CH1
PB7.Signal=S_TIM4_CH2
PB8.Signal=S_TIM4_CH3
PB9.Signal=S_TIM4_CH4
PC13-ANTI_TAMP.GPIO_Label=LED
PC13-ANTI_TAMP.Signal=GPIO_Output
PC14-OSC32_IN.Signal=RCC_OSC32_IN
PC15-OSC32_OUT.Signal=RCC_OSC32_OUT

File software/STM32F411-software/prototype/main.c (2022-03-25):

#include <stdio.h>
#include <stdint.h>
#include <stdbool.h>

enum Peripheral {
    STM32_CONFIG            = 0,
    MOTOR_CONTROL           = 1,
    LED                     = 2,
    LEAK_DETECTOR           = 3,
    TEMPERATURE_SENSOR      = 4,
    PRESSURE_SENSOR         = 5,
    RADIATION_SENSOR        = 6,
    CHLOROPHYLL_SENSOR      = 7,
    ACCELERATION_SENSOR     = 8,
    GYROSCOPE_SENSOR        = 9,
    MAGNETOMETER_SENSOR     = 10,
    CURRENT_MEASUREMENT     = 11,
    HYDROPHONE_SENSOR       = 12,
    NOT_RECOGNIZED = 0xff
};

struct command
{
    enum Peripheral peripheral;
    bool RW;
    uint8_t type;
    uint8_t channel;
    uint16_t data;
};

enum Peripheral getPeripheral(char peripheralByte)
{
    if (peripheralByte <= 13)
        return (enum Peripheral) peripheralByte;
    return NOT_RECOGNIZED;
}

void decodeMessage(struct command *cmd, char *buf, int size)
{
    cmd->peripheral = getPeripheral(buf[0]);
    cmd->RW      =  (buf[1] & 0b10000000) >> 7;
    cmd->type    =  (buf[1] & 0b01100000) >> 6;
    cmd->channel =  (buf[1] & 0b00011111);
    cmd->data    = (buf[2] << 8) + buf[3];
}


int main()
{
    char buf[] = {'\x00', '\x00', '\x00', '\x00'};
    struct command msg;
    decodeMessage(&msg, buf, 4);
    printf("Peripheral : %d\n", msg.peripheral);
    printf("Read/Write : %d\n", msg.RW);
    printf("Type : %d\n", msg.type);
    printf("channel : %d\n", msg.channel);
    printf("data : %d\n", msg.data);

    return 0;
}

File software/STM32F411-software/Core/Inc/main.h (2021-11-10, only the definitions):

#define LED_Pin GPIO_PIN_13
#define LED_GPIO_Port GPIOC
#define LED2_Pin GPIO_PIN_2
#define LED2_GPIO_Port GPIOB
#define LED3_Pin GPIO_PIN_12
#define LED3_GPIO_Port GPIOB
#define SPI_CS_Pin GPIO_PIN_8
#define SPI_CS_GPIO_Port GPIOA
#define ACCEL_INT_Pin GPIO_PIN_15
#define ACCEL_INT_GPIO_Port GPIOA
#define GYRO_INT_Pin GPIO_PIN_4
#define GYRO_INT_GPIO_Port GPIOB
#define MAG_INT_Pin GPIO_PIN_5
#define MAG_INT_GPIO_Port GPIOB

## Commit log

2021-07-18 Software : entrypoint STM32G4, raspberry pi streaming, IMU experiments ; Hardware : stm32g4 board, radiation/chlorophyll sensor, motor driver
    [ABLS.STEP, EEU-FR1E151.stp, PCB1.PcbDoc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]
2021-09-12 g4 software ; madgwick filter working experiment ; communication over ethernet test
2021-09-15 camera streaming (tested and working 1920x1020 30fps reasonably low latency)
2021-10-11 Mechanical design v1 by Tigran
    [25 mm Standoff.SLDPRT, Bottom Frame.SLDPRT, Bracket Holder Botoom.SLDPRT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]
2021-11-03 motor driver
    [motor_driver_v1-B_Cu.gbr, motor_driver_v1-B_Mask.gbr, motor_driver_v1-B_Paste.gbr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]
2021-11-07 final boards, radiation sensor
    [BMI088.stp, IIS2MDCTR.stp, LSM303AGRTR.stp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]
2021-11-10 added render of final ROV board
2021-12-10 UART communication
    [TC4424AVOA.stl, TC4424AVOA.stp, flight-controller.kicad_pcb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]
2022-02-04 hardware, please final
    [Channel1.kicad_sch, Channel2.kicad_sch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]
2022-03-25 softw update
    [LED-B_Cu.gbr, LED-B_Mask.gbr, LED-B_Paste.gbr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]

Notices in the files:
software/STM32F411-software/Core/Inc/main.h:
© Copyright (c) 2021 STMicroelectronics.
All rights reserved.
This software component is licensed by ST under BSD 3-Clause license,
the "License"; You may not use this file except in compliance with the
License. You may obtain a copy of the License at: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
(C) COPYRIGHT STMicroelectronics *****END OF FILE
